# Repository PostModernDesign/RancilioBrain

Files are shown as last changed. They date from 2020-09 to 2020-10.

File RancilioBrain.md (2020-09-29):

### This is a work in progress

# Interface Parts
InstallationRender
partStack

You certainly dont need to puchase these components from amazon, you can find them on ebay or banggood or aliexpress as well. It's usually worth it to get a few of the same because it's easy to ruin them during prototyping. 

1 [5.08mm Pitch Screw Terminals](https://www.amazon.com/gp/product/B07DQNVLL8/ref=ppx_yo_dt_b_search_asin_title?ie=UTF8&psc=1)
2 [128 x 64 OLED](https://www.amazon.com/gp/product/B085WCRS7C/ref=ppx_yo_dt_b_search_asin_title?ie=UTF8&psc=1)
4 [Perf Board](https://www.amazon.com/Solderable-BreadBoard-matches-breadboards-1-85in/dp/B00LLO4Q7W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)
5 [120v AC to 5v DC](https://www.amazon.com/gp/product/B07YXN8J6R/ref=ppx_yo_dt_b_search_asin_title?ie=UTF8&psc=1)
6 [Large Aluminum Knob](https://www.amazon.com/gp/product/B087M2QCC2/ref=ppx_yo_dt_b_search_asin_title?ie=UTF8&psc=1)
7 [Rotary Encoder](https://www.amazon.com/gp/product/B07DM2YMT4/ref=ppx_yo_dt_b_search_asin_title?ie=UTF8&psc=1)
8 [Arduino Nano](https://www.amazon.com/gp/product/B07KCH534K/ref=ppx_yo_dt_b_search_asin_title?ie=UTF8&psc=1)
11 [2.54mm Pitch Screw Terminals](https://www.amazon.com/gp/product/B07NSJV6NW/ref=ppx_yo_dt_b_search_asin_title?ie=UTF8&psc=1)

# Other Parts
SSRs

Besides the enclosure assembly, you will need suitable wire, various [spade connectors](https://www.amazon.com/gp/product/B078PMWNJC/ref=ppx_yo_dt_b_search_asin_title?ie=UTF8&psc=1) and 2 quality [40A Relays](https://www.amazon.com/gp/product/B00E1LC1VK/ref=ppx_yo_dt_b_search_asin_title?ie=UTF8&psc=1). I've used 200ºC Temp resistant silicone wire for all lengths runnning inside the machine, [18AWG](https://www.amazon.com/gp/product/B0746HMTPP/ref=ppx_yo_dt_b_search_asin_title?ie=UTF8&psc=1) for the relays and [22AWG](https://www.amazon.com/gp/product/B01M0O1NXM/ref=ppx_yo_dt_b_search_asin_title?ie=UTF8&psc=1) for the 5V signal wires.
wiring diagram
You will also need to reroute the ground to the 3 way valve so that solenoid if you plan to have solenoid control independent of pump control like I do. Otherwise just piggyback the poles of the brew switch.

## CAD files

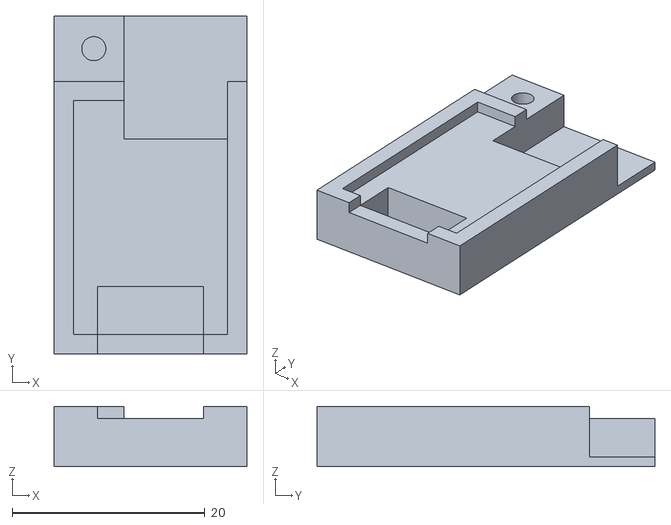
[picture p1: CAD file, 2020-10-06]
3D_Printables_WIP(NOT_Perfect)/hx711 enclosure/HX711Bottom.stl
20.0 x 35.0 x 6.25

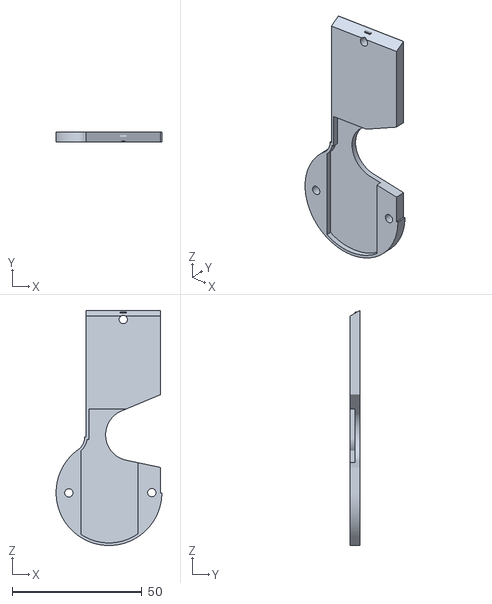
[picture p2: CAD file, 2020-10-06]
3D_Printables_WIP(NOT_Perfect)/Lid-largerWireHole.stl
40.8 x 4.00 x 90.6

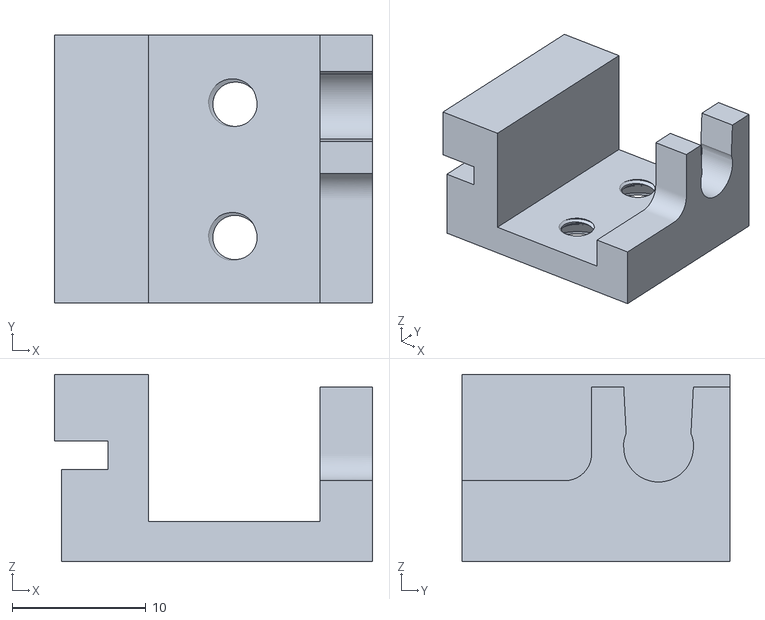
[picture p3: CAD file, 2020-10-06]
3D_Printables_WIP(NOT_Perfect)/load SensorMounts/LeftLoadSensorV6.stl
23.8 x 20.0 x 14.0

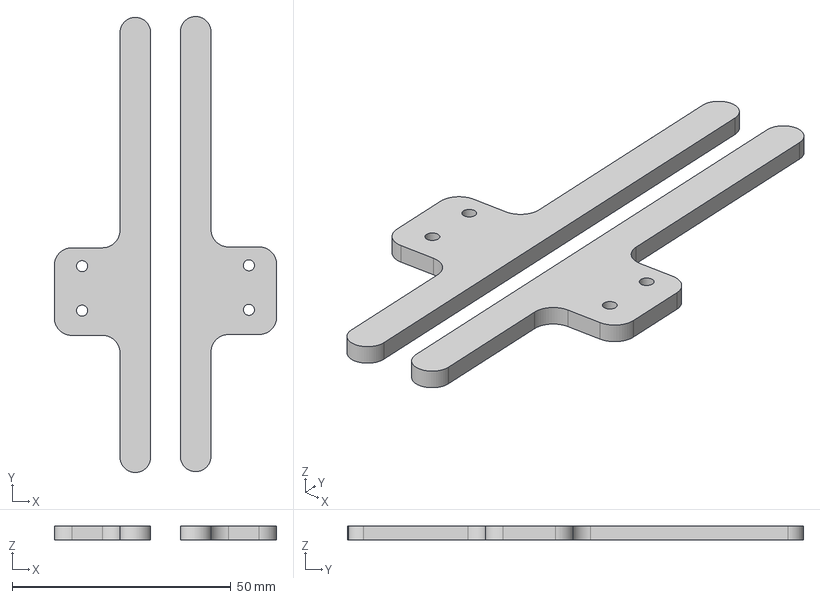
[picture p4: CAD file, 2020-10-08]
LoadCellTrayFeet.step
50.8 x 104.1 x 3.25 mm

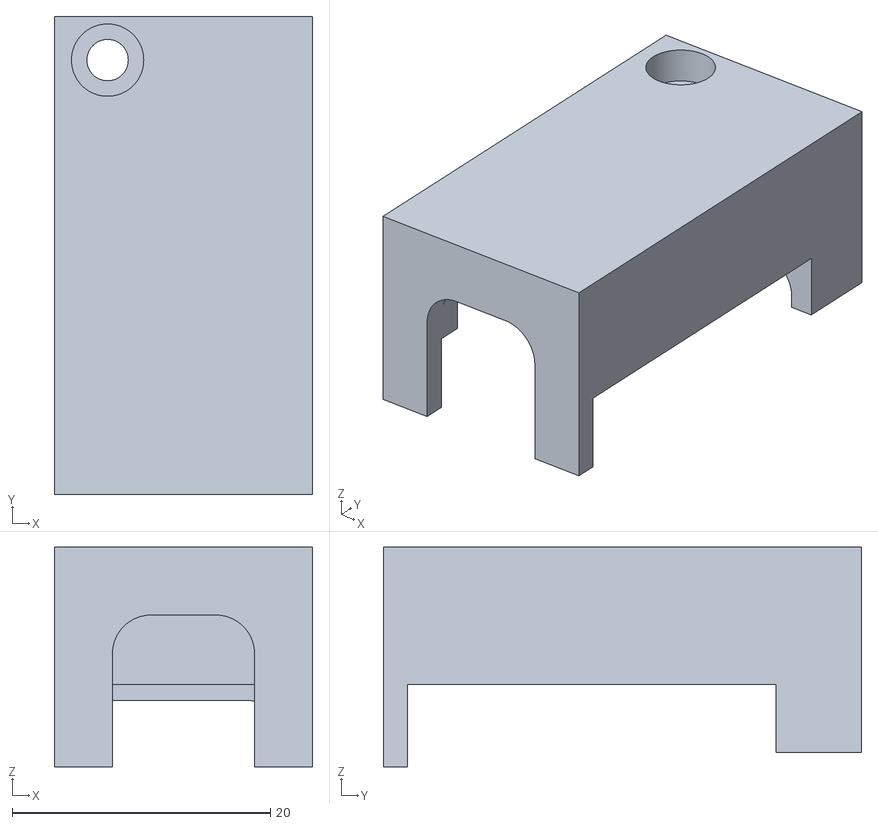
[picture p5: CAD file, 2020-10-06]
3D_Printables_WIP(NOT_Perfect)/hx711 enclosure/hx711Top.stl
20.0 x 37.0 x 17.0

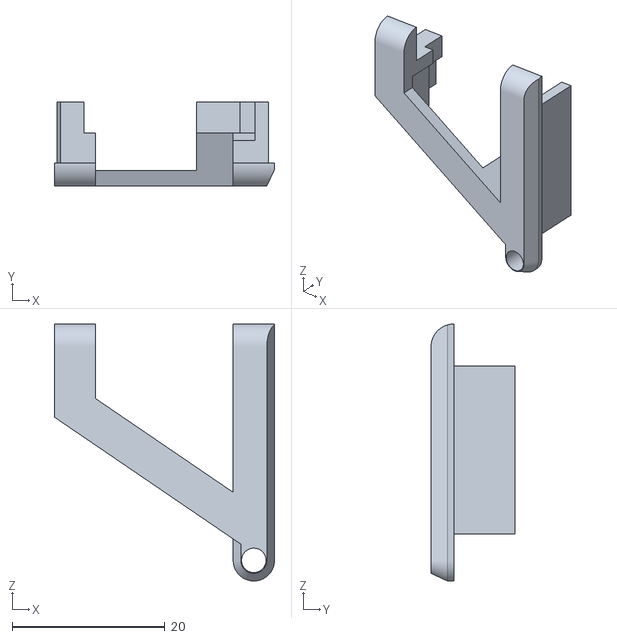
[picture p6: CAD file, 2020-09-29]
3D_Printables_WIP(NOT_Perfect)/timerScreenClip.stl
28.8 x 11.0 x 33.7

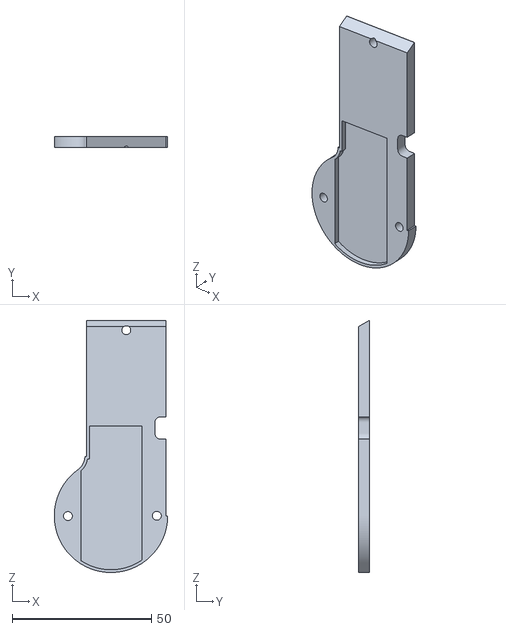
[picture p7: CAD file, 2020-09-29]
3D_Printables_WIP(NOT_Perfect)/lidv4.stl
40.8 x 4.00 x 90.6

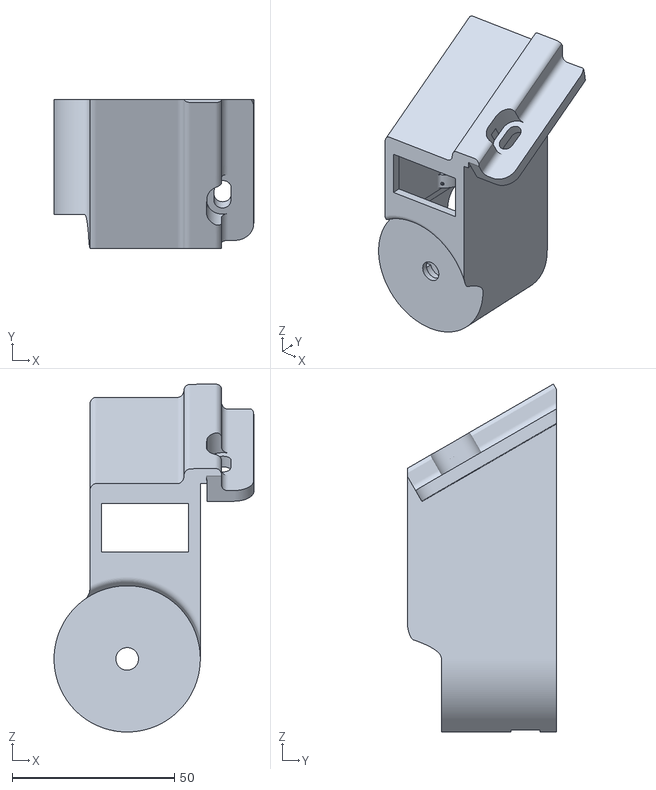
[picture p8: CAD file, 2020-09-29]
3D_Printables_WIP(NOT_Perfect)/enclosureWITHRIB.stl
61.5 x 46.0 x 107.1

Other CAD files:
3D_Printables_WIP(NOT_Perfect)/load SensorMounts/RightLoadSensorV6.stl

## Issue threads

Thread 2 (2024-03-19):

adding a PID control 🤔 🙏

RE-Specto, 2024-03-19:
how about adding a PID control to your code? you already have SSR, MCU, LCD.. the only part missing is a thermocouple and some coding.
great idea about the weight though.. can you post the weight sensor mounting system please? 🙏

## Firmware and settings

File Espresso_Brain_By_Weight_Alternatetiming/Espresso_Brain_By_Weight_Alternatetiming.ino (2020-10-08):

//FYI I used this hx711 library 
//     URL: https://github.com/RobTillaart/HX711


//Screen Stuff
#include <Adafruit_SSD1306.h>
//#include <splash.h>
#define SCREEN_WIDTH 128
#define SCREEN_HEIGHT 64
#define OLED_RESET     4 // Reset pin # (or -1 if sharing Arduino reset pin)
Adafruit_SSD1306 display(SCREEN_WIDTH, SCREEN_HEIGHT, &Wire, OLED_RESET);

#include <EEPROM.h> //This is being used to store the target weight so when arduino power cycles it retains last used weight

//this is the little board that comes with each load cell
#include "HX711.h"
HX711 scale;
HX711 scale2;

// pins for the first load cell
uint8_t dataPin = 5;
uint8_t clockPin = 6;

// pins for the second load cell
uint8_t dataPin2 = 11;
uint8_t clockPin2 = 12;

//the variable to hold a value for each load cell (float because it is a decimal)
float w1;
float w2;

//Obviously we use this stuff for weight
float currentWeight;
float lastWeight;
bool weightReached = false;
float targetWeight;
float weightOffset = 1.2; // This value is how many grams before the target should the pump shut off, you need to test

//This stuff is all related to timing
const unsigned long eventInterval = 100; 
const unsigned long reachedInterval = 3000; // how long to keep reading and updating the weight after the target weight is reached (btw 1000 = 1s)
unsigned long previousTime = 0;
unsigned long startCounting; 
float elapsedTime;
unsigned long currentTime;
float tV = 0.0;

//This is the weight that arduino will default to when powered on
int storedWeight;


//This is rudamentary state logic
bool started = false;
bool preStarted = false;


//-------------- the rotary encoder  //--------------
int buttonPin = 4;
int buttonPinState = 1;
int buttonPinLast = 1;
bool buttonPressed = 0;
int pinA =3; 
int pinB = 2;
int pinAStateCurrent = HIGH;
int pinAStateLast = pinAStateCurrent;
bool turnDetected = false;


//-------------- The Relays //--------------
int threeWay = 9;
int pump = 10;

//Helper functions that turn the relays on and off 
void extractOn(){
  digitalWrite(pump, HIGH);
  digitalWrite(threeWay, HIGH);
  }

void extractOff(){
  digitalWrite(pump, LOW);
  digitalWrite(threeWay, LOW);
  }



//-------------- These are the different layouts for each screen that we will use, helps keep our code more readable to break them out like this//-------------- 


//When you first turn the machine on
void preStartedDisplay(){
  display.setTextSize(1);     
  display.setTextColor(SSD1306_WHITE); // Draw white text
  display.setCursor(0, 0);   
  display.print("Target Weight");
  display.setTextSize(3);     
  display.setTextColor(SSD1306_WHITE); // Draw white text
  display.setCursor(0, 14);   
  display.print(targetWeight, 1);


//if you've pulled a shot already put the info on screen (if TV isnt 0 you've pulled a shot)  
  if (tV !=0){   
    display.setTextSize(1); // this is size..  1 is 8 pixels tall, 2 is 16, and so on
    display.setTextColor(SSD1306_WHITE); // Draw white text
    display.setCursor(0, 44); // this is position in (x,y)
    display.print("Previous Weight"); //display.print sends this to buffer
    display.setTextSize(1);     
    display.setTextColor(SSD1306_WHITE); // Draw white text
    display.setCursor(98, 44);   
    display.print(lastWeight, 1);
    display.setTextSize(1);     
    display.setTextColor(SSD1306_WHITE); // Draw white text
    display.setCursor(0, 56);
    display.print("Previous Time");
    display.setTextSize(1);     
    display.setTextColor(SSD1306_WHITE); // Draw white text
    display.setCursor(98, 56);   
    display.print(tV, 1);
  }
}

//-------------- when the shot is being pulled this is what is shown
void startedDisplay(){

  display.setTextSize(1);     
  display.setTextColor(SSD1306_WHITE); // Draw white text
  display.setCursor(0, 0);   
  display.print("Target Weight");
  display.setTextSize(1);     
  display.setTextColor(SSD1306_WHITE); // Draw white text
  display.setCursor(85, 0);   
  display.print(targetWeight, 1);
  display.setTextSize(2);     
  display.setTextColor(SSD1306_WHITE); // Draw white text
  display.setCursor(0,22);   
  display.print("Weight");
  display.setTextSize(2);     
  display.setTextColor(SSD1306_WHITE); // Draw white text
  display.setCursor(80,22);   
  display.print(currentWeight, 1);
  display.setTextSize(2);     
  display.setTextColor(SSD1306_WHITE); // Draw white text
  display.setCursor(0, 46);   
  display.print("Time");
  display.setTextSize(2);     
  display.setTextColor(SSD1306_WHITE); // Draw white text
  display.setCursor(80, 46);   
  display.print(tV,1);


  }

//-------------- This is identical to when a shot is pulled only we switch to a more precise method of reading the scale (called lastWeight)

void justEndedDisplay(){
  display.setTextSize(1);     
  display.setTextColor(SSD1306_WHITE); // Draw white text
  display.setCursor(0, 0);   
  display.print("Target Weight");
  display.setTextSize(1);     
  display.setTextColor(SSD1306_WHITE); // Draw white text
  display.setCursor(85, 0);   
  display.print(targetWeight, 1);
  display.setTextSize(2);     
  display.setTextColor(SSD1306_WHITE); // Draw white text
  display.setCursor(0,22);   
  display.print("Weight");
  display.setTextSize(2);     
  display.setTextColor(SSD1306_WHITE); // Draw white text
  display.setCursor(80,22);   
  display.print(lastWeight, 1);
  display.setTextSize(2);     
  display.setTextColor(SSD1306_WHITE); // Draw white text
  display.setCursor(0, 46);   
  display.print("Time");
  display.setTextSize(2);     
  display.setTextColor(SSD1306_WHITE); // Draw white text
  display.setCursor(80, 46);   
  display.print(tV,1);

  }


//-------------- This is just that text "starting" that appears after you click the encoder but before the pump is on.


void startingDisplay(){
  display.clearDisplay();
  display.setTextSize(2);     
  display.setTextColor(SSD1306_WHITE); // Draw white text
  display.setCursor(15,18);   
  display.print("Starting");
  display.display();
  }


//-------------- This function adds or subtracts .1 to the target weight if you turn left or right
void increment(){
    turnDetected = true;
    //Rotation
    pinAStateCurrent = digitalRead(pinA);
    if((pinAStateLast == LOW) && (pinAStateCurrent == HIGH)){
    if(digitalRead(pinB) == HIGH){
          Serial.println("decremented");
          targetWeight -= 0.1;
        delay(15);
      }
    else {
    targetWeight += 0.1; 
    delay(15);
    }
  }
  pinAStateLast = pinAStateCurrent;
}

//--------------  This function checks to see if the button was pressed
void buttonDetect(){
  buttonPinState=digitalRead(buttonPin);
  if (buttonPinState != buttonPinLast){
     if ((buttonPinState==1) && (!started)) /*I just started extracting*/{
      preStarted = false;
      startingDisplay();
      tareScales();
      delay(250);
      tV=0;
      currentWeight=0;
      elapsedTime=0;
      preStarted = false;
      started=true;
      extractOn();
      startCounting = millis();
      display.clearDisplay();
      }
     if ((elapsedTime>1.0) &&(buttonPinState==1) && (started)) /*I want to stop the extraction manually*/{
      weightReached = true;
      }
    buttonPinLast=buttonPinState;
  }
}
//-------------- This is the interupt that we create in our setup, the conditional statement means if you rotate the encoder while a shot is extracting it wont run any code and cause lag

void update(){
  if(preStarted) {
    increment();
  }
}

//--------------//--------------//--------------//--------------//--------------//--------------//--------------//--------------//--------------
//--------------//--------------//--------------//--------------//--------------//--------------//--------------//--------------//--------------

void setup()
{
  Serial.begin(9600);
  
//display setup
    if(!display.begin(SSD1306_SWITCHCAPVCC, 0x3C)) { // Address 0x3C for 128x32
    Serial.println(F("SSD1306 allocation failed"));
    for(;;); // Don't proceed, loop forever
  
  }

//This is seeing if this is the first time you are writing to the eeprom and if it is just put a 0 for now
  if (EEPROM.read(256) != 123){
    EEPROM.write(256, 123);
    storedWeight = 0;
  }

//This code runs every time the arduino powers back on... it sets the target weight to the last weight used so that it "remmbers"
  else {
    EEPROM.get(0, storedWeight);  
  }
//  This is a trick to convert our int back into a float, eeprom floats cant go very high because you only have like a byte so we store the weigth as an int and convert it back 
  targetWeight = storedWeight*0.1;

//setting up the relays
   pinMode (pump, OUTPUT);
   pinMode(threeWay, OUTPUT);

//making sure the pump and valve are off, probably dont need but just in case   
   extractOff();

// inital display 
  display.clearDisplay();
  preStartedDisplay();
  display.display();

//  This is our rotary encoder setup
  pinMode(buttonPin, INPUT_PULLUP); // initialize the button pin as a input
  pinMode (pinA, INPUT_PULLUP);
  pinMode (pinB, INPUT_PULLUP);
  attachInterrupt(digitalPinToInterrupt(pinA), update, CHANGE);


//  This initiallizes the scales
  scale.begin(dataPin, clockPin);
  scale2.begin(dataPin2, clockPin2);

//This is the callibration value for each load cell, you need to calibrate 
//them with a known weight The good thing is that the value is linear so if 
//you know somethign weights 100g you can calculate what the value should be. 
  scale.set_scale(1091); 
  scale2.set_scale(1105);

//set the scales to 0
  scale.tare();
  scale2.tare();

//Set the state of the system
  preStarted = true;
}

//--------------//--------------//--------------//--------------//--------------//--------------//--------------//--------------//--------------//--------------
//--------------//--------------//--------------//--------------//--------------//--------------//--------------//--------------//--------------//--------------

void loop(){

//check to see if extraction is running and perform a get weigth if it is
    if ((preStarted == false) && (!weightReached)){
        scaleFunc();
    }
// check to see if the shot just ended and switch to doing multiple averaged readings for more accuracy
    if ((preStarted == false) && (weightReached)){
        precisionScale();
    }


  currentTime = millis();
//check if button is pressed and run the button detect code we defined earlier 
  buttonDetect();

//  ––––––––––––––––––––––––––––––––––––––––

//This is the code that updates the time and weight value while the extraction is happening
  if(started){
      if(!weightReached){
          elapsedTime = ((currentTime - startCounting)*.001);
          tV = elapsedTime;
        previousTime = currentTime;
        display.clearDisplay();
        startedDisplay();
        display.display();      
        }
  }

//  ––––––––––––––––––––––––––––––––––––––––  

//This is the code that updates the weight for a few more moments just after the shot has stopped extracting and timer has stopped
  if (weightReached && started){
    extractOff();
    display.clearDisplay();
    justEndedDisplay();
    display.display(); 
  if(currentWeight>lastWeight){
      lastWeight = currentWeight;
      }
    }
  //This is the code that goes back to the inial standby screen when you are finished extracting so you can set another weight
  if(!started){
    display.clearDisplay();
    preStartedDisplay();
    display.display();
  }


//This is the code to stop the extraction once the target weight is reached. 
//I added the conditional to only runs 5s after extraction starts because 
//sometimes you need to reposition your cup and that would trip 
//the weight and stop extraction and ruin your shot :(

  if (tV>5){
    if ((currentWeight) > (targetWeight-weightOffset)){
       lastWeight=currentWeight;
       weightReached = true;
        if (storedWeight != round(targetWeight/0.1)) {
          storedWeight= round(targetWeight/0.1); 
          EEPROM.put(0, storedWeight);
          }
    }
  }

//  this code runs after your weight is reached AND a certain extra 
//amount of time has passed, you know for the last few drips... 
//it resets the states so you are ready to brew again... 
// e.g you can change it to 5s if you update your reached interval value to 5000 at the top.
    if( currentTime - previousTime >= reachedInterval){
        started=0;
        weightReached = false;
        preStarted = true;
        currentWeight=0;
        }


//  Post pump shutoff / residual flow compensation (WIP) ––––––––––––––––––––––––––––––––––––––––        

//the idea behind this is if your shot is reaching weight quickly, cut the pump more grams before the target weight
//and the other way around, if your shot is coming out slow, only cut the pump just before the target. 
// There is a smarter way to do this, I haven't discoverd it yet.

 if (tV <= 20){
  weightOffset = 3.0;
  }   
 if ((tV >20) && (tV<= 22)){
  weightOffset = 1.9;
  }   
 if ((tV >22) && (tV<= 24)){
  weightOffset = 1.5;
  }   
 if ((tV >24) && (tV<= 26)){
  weightOffset = 1.2;
  }   
 if ((tV >26) && (tV<= 28)){
  weightOffset = 1;
  }   
 if ((tV >28) && (tV<= 30)){
  weightOffset = .9;
  }   
 if ((tV >30) && (tV<= 33)){
  weightOffset = 1;
  }   
 if (tV >33){
  weightOffset = .75;
  }   

    
}//This is the end of our loop

//--------------//--------------//--------------//--------------//--------------//--------------//--------------//--------------//--------------//--------------
//--------------//--------------//--------------//--------------//--------------//--------------//--------------//--------------//--------------//--------------

//A few helper functions

//This asks the scales to get the weight and add them up 
void scaleFunc(){
  w1 = scale.get_units();
  w2 = scale2.get_units();
  if((w1+w2)>1){
    currentWeight=(w1+w2);
   }
}
//This asks the scales to check the weight twice so in theory its more accurate, this is how the shot is weighed just after the pump is off
void precisionScale(){
  w1 = scale.get_units(2);
  w2 = scale2.get_units(2);
  currentWeight= (w1+w2);
  }

//We tare the cells just after the rotary knob is clicked, this helper function is almost not worth writing, but whatevs
void tareScales(){
  scale.tare();
  scale2.tare();
  }

//--------------

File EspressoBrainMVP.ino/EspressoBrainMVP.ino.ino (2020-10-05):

/*
––––––––––––––––––––––
Espresso Timer Intention
––––––––––––––––––––––


___  Current Functions ___ 
– Set a brew time- turn on pump, open solenoid, count down on OLED, Turn off pump close solenoid.

___  Future Functions ___ 
– Menu to change modes and change parameters 
– Optize code becuase running out of space
– Set a preinfusion time and delay time – Open Solenoid, count, close solenoid, count, turn on pump, open solenoid, count down, etc..
– Backflush Mode - 15sec on, 15 sec rest - 5 times
– Manual Mode - Start pump and count up
– Wire up Load Cells
– Target weight mode - set weight and brew up until that weight.
*/

//1st order variables and functions
bool setupDone=0;
bool timerRunning = 0;
#include <EEPROM.h> 


/*–––––––––––––––––––––––––––––
Display Setup
–––––––––––––––––––––––––––––*/
#include <Adafruit_SSD1306.h>
#include <splash.h>
#define SCREEN_WIDTH 128
#define SCREEN_HEIGHT 64
#define OLED_RESET     4 // Reset pin # (or -1 if sharing Arduino reset pin)
Adafruit_SSD1306 display(SCREEN_WIDTH, SCREEN_HEIGHT, &Wire, OLED_RESET);


//LayoutFunctions
void topLeftLabel(String j) {
  display.setTextSize(2);      // scale 2
  display.setTextColor(SSD1306_WHITE); // Draw white text
  display.setCursor(0, 0);     // Start at top-left corn
  display.print(j);
  }

void middleLeftTime(float j) {
  display.setTextSize(5);      // scale 5
  display.setTextColor(SSD1306_WHITE); // Draw white text
  display.setCursor(0, 24);     // these are coordinates(x, y)
  display.print(j, 1); // in this sketch this parameter is the time value aka (tV)
  }


/*–––––––––––––––––––––––––––––
Encoder Setup
–––––––––––––––––––––––––––––*/


//Tactile Switch Setup
int buttonPin = 4;
int buttonPinState = 1;
int buttonPinLast = 1;
bool buttonPressed = 0;


//Tactile Switch Detection---------------
void buttonDetect(){
  buttonPinState=digitalRead(buttonPin);
  if (buttonPinState != buttonPinLast){
     if ((buttonPinState==1) && (timerRunning==0)){
      buttonPressed=1;
      extractOn();
      }
    buttonPinLast=buttonPinState;
  }
}

//Rotary Encoder Turn Detection
//you need to use these pins because the support interupt
int pinA = 3;
int pinB = 2;
int pinAStateCurrent = LOW;
int pinAStateLast = pinAStateCurrent;
bool turnDetected = false;
 
/*–––––––––––––––––––––––––––––
Timer Setup
–––––––––––––––––––––––––––––*/
//millis Function

const unsigned long eventInterval = 100;
unsigned long previousTime =0;
int storedTime;
float tV;
float countDownDefault;



/*–––––––––––––––––––––––––––––
Menu Setup
–––––––––––––––––––––––––––––*/
//to do one day


/*–––––––––––––––––––––––––––––
Relay Setup
–––––––––––––––––––––––––––––*/

int threeWay = 9;
int pump = 10;

void extractOn(){
  digitalWrite(pump, HIGH);
  digitalWrite(threeWay, HIGH);
  }

void extractOff(){
  digitalWrite(pump, LOW);
  digitalWrite(threeWay, LOW);
  }



//update encoder function
void rotaryIncrement(){
    turnDetected = true;
    //Rotation
    pinAStateCurrent = digitalRead(pinA);
    if((pinAStateLast == LOW) && (pinAStateCurrent == HIGH)){
    if(digitalRead(pinB) == HIGH){
        if(tV>=.1){
          tV-= 0.1;
        }
        countDownDefault = tV;
//        storedTime=countDownDefault/0.1; 
        delay(15);
      }
    else {
    tV += 0.1;
    countDownDefault = tV;
//    storedTime=countDownDefault/0.1; 
    delay(15);
    }
  }
  pinAStateLast = pinAStateCurrent;
}

void update(){
  if((!timerRunning) && (setupDone)) {
    rotaryIncrement();
  }
  else{
//    Serial.println("ignored input, timer is running");
    }
}





void setup() {
  Serial.begin(9600);
//display setup
    if(!display.begin(SSD1306_SWITCHCAPVCC, 0x3C)) { // Address 0x3C for 128x32
    Serial.println(F("SSD1306 allocation failed"));
    for(;;); // Don't proceed, loop forever
  }


if (EEPROM.read(256) != 123){
  EEPROM.write(256, 123);
  storedTime = 0;
  }
 else {
  EEPROM.get(0, storedTime);
 }
  tV = storedTime*0.1;

//  tactile setup
  pinMode (buttonPin, INPUT_PULLUP);
  display.clearDisplay();
  topLeftLabel("Shot Time");
  middleLeftTime(tV);
  display.display();



//Rotary Setup
  pinMode (pinA, INPUT_PULLUP);
  pinMode (pinB, INPUT_PULLUP);
  pinMode (buttonPin, INPUT_PULLUP);
  attachInterrupt(digitalPinToInterrupt(pinA), update, CHANGE);
  countDownDefault = tV;
 
 //SSR Setup
 pinMode (pump, OUTPUT);
 pinMode(threeWay, OUTPUT);
 extractOff();
  setupDone=1;

}




void loop() {

if (turnDetected){
  turnDetected=false;
  display.clearDisplay();
  topLeftLabel("Shot Time");
  middleLeftTime(tV);
  display.display();
  }

//buttonDetection
  buttonDetect();
  /* Updates frequently */
  unsigned long currentTime = millis();
if(buttonPressed){
  timerRunning=1;
  
  if( currentTime - previousTime >= eventInterval){
    if(tV >= 0.1){
      tV -= 0.1;
      previousTime = currentTime;
      display.clearDisplay();
       topLeftLabel("Extracting");
      middleLeftTime(tV);
      display.display();
    }
    else  {
      display.clearDisplay();
      topLeftLabel("Extracting");
      middleLeftTime(0.0);
      display.display();
      extractOff();
//      Serial.println("End countDownDefault: ");
//      Serial.println(countDownDefault);
//      Serial.println("storedTime: ");
//      Serial.println(storedTime);
      timerRunning=0;
      tV=countDownDefault; 
      if (storedTime != round(countDownDefault/0.1)) {
        storedTime = round(countDownDefault/0.1); 
        EEPROM.put(0, storedTime);
//        Serial.println("yes EEPROM: ");
//        Serial.println(storedTime);
        }
      delay(1000);
      buttonPressed=0;
      display.clearDisplay();
      topLeftLabel("Shot Time");
      middleLeftTime(tV);
      display.display();
     }
  }
}
}

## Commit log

2020-09-29 Arduino Sketch + Files
    These are rough, not an expert
    [enclosureWITHRIB.stl, lidv4.stl, timerScreenClip.stl]
2020-10-06 uploaded some more 3D printer files
    [HX711Bottom.stl, LeftLoadSensorV6.stl, Lid-largerWireHole.stl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]
2020-10-08 Add files via upload
    These are 3D files if you want cut feet for the load cells out of aluminum. Send them to a place like 3D hubs - https://www.3dhubs.com - and they will ship them to you... the holes should be tapped w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
    [LoadCellTrayFeet.step]
